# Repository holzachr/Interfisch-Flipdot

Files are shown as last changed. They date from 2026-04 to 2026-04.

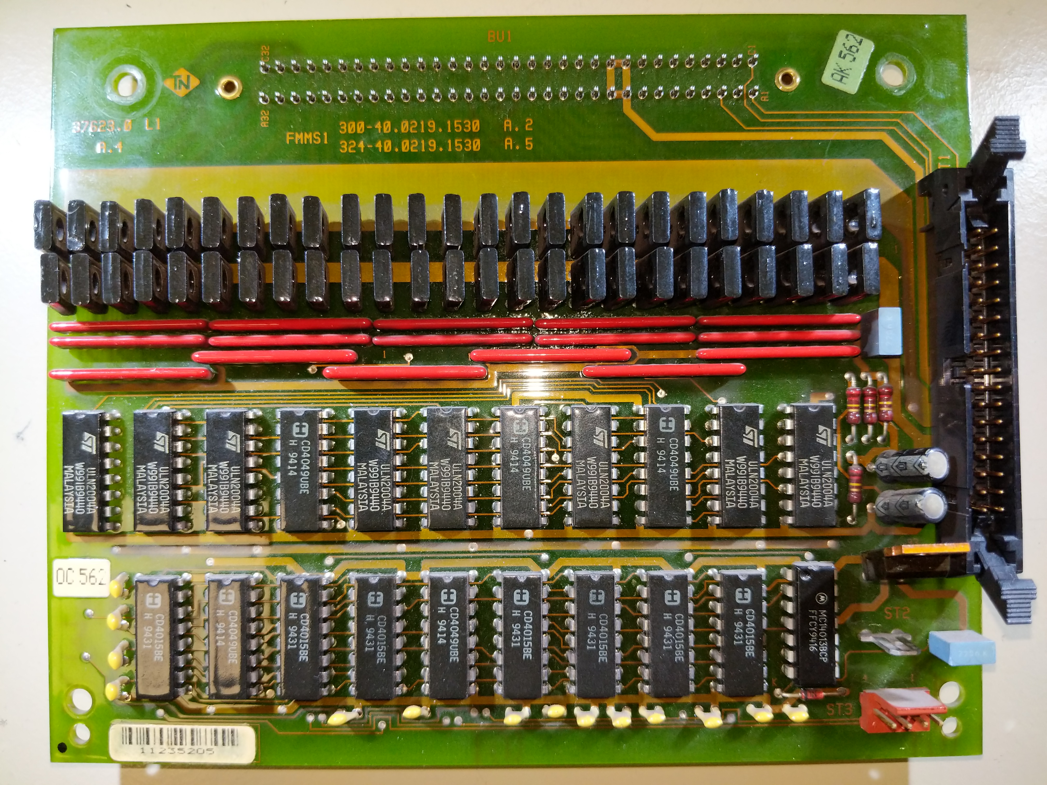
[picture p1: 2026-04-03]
reverseengeneering/annax37623_front.jpg

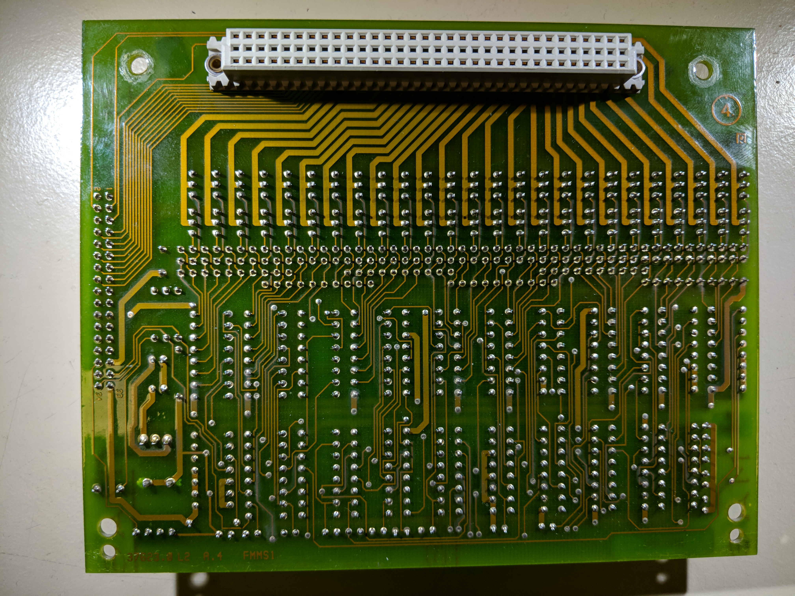
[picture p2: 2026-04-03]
reverseengeneering/annax37623_back_unlit.jpg

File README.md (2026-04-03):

This is a fork of "Interfisch"'s brilliant work for creating an ESP32 based "Annax" flipdot module controller board, software and more.

The goals of this fork are
- Re-layouting the controller board to fit the original ADtranz controller board
- Modifying the ESP32 software to support the original ADtranz flipdot module configuration (2x 25x16, 2x 20x16, 1x 25x16)
- Added another useful test pattern (checkers)
- Made flipdot timing parameters settable through MQTT, to help determine ideal settings

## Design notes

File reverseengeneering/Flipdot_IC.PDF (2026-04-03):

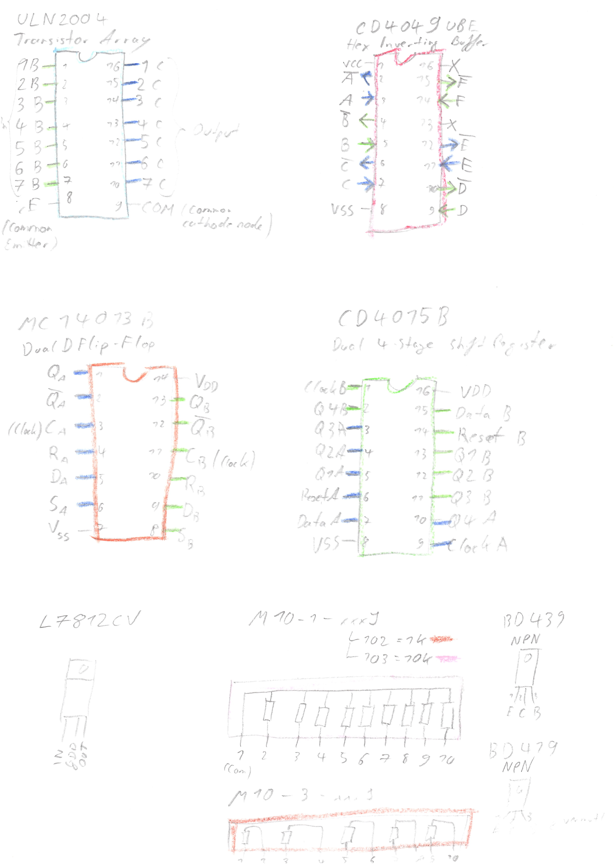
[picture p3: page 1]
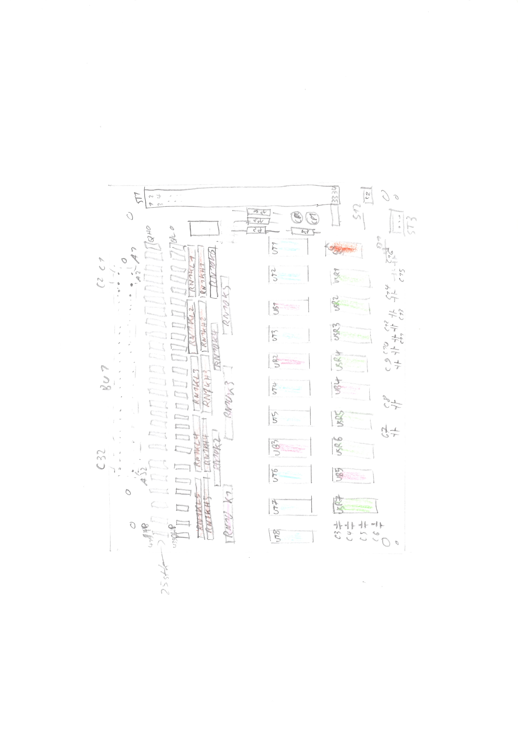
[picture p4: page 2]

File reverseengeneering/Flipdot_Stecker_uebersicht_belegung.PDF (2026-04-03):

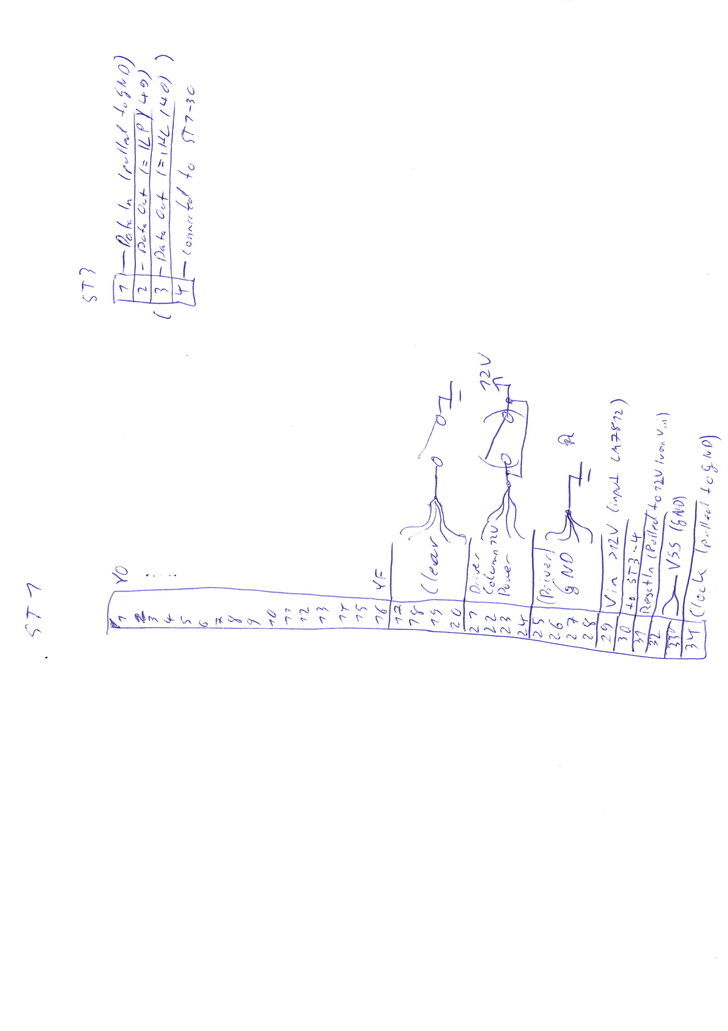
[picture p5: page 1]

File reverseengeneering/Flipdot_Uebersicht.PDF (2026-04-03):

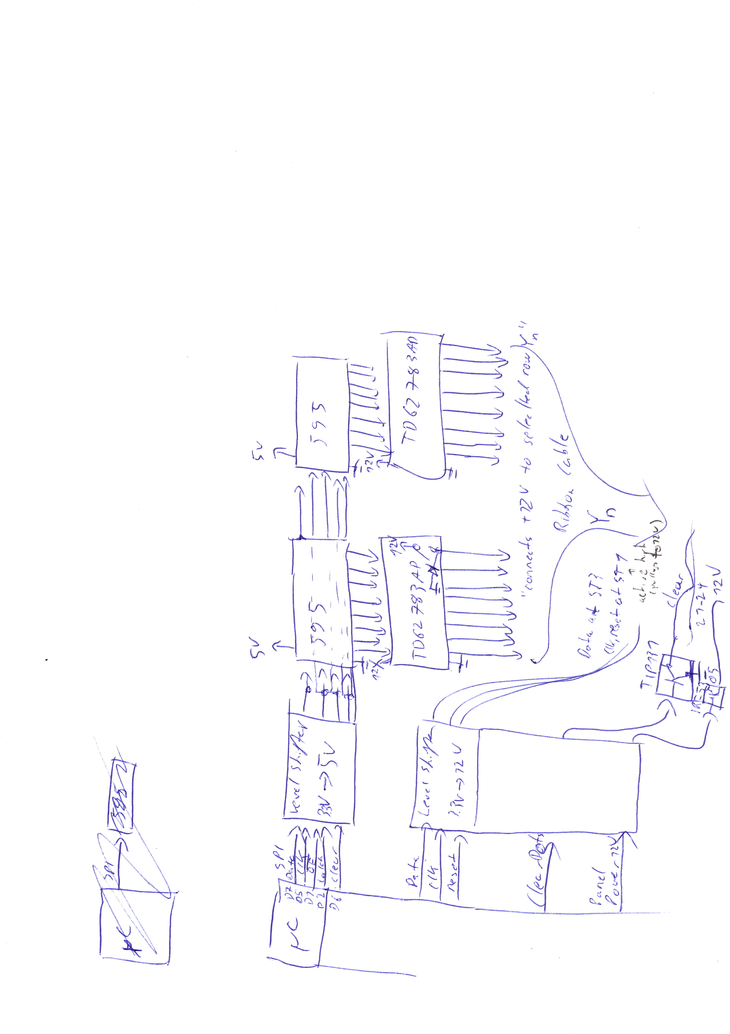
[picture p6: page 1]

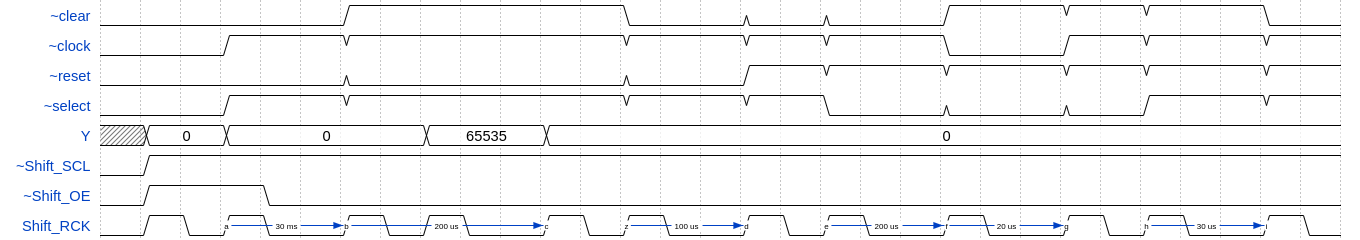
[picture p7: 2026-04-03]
reverseengeneering/control_initialize_timingdiagram_wavedrom.png

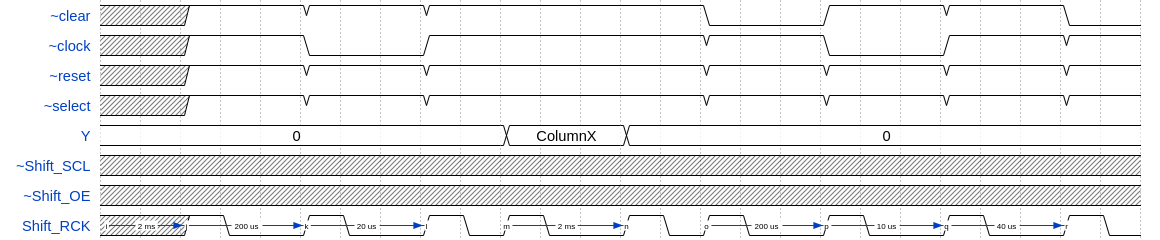
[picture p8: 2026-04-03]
reverseengeneering/control_renderColumn_timingdiagram_wavedrom.png

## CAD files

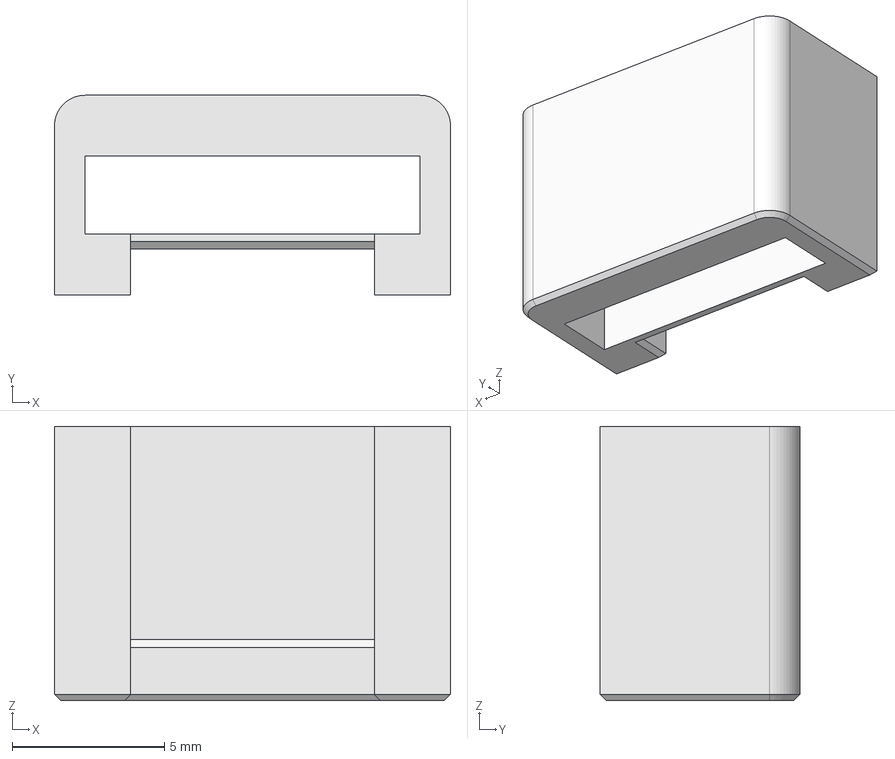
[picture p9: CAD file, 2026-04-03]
CAD/4Pin_DataConnector_Housing.FCStd
13.0 x 6.55 x 9.00 mm

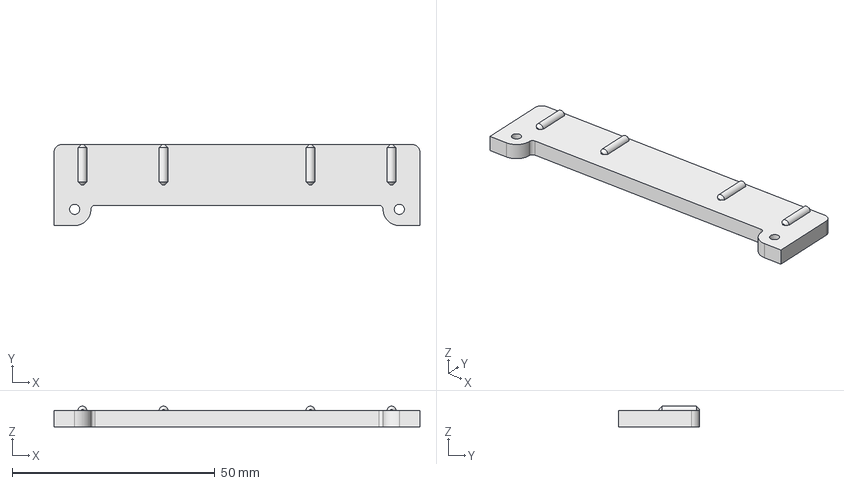
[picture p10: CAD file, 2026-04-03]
CAD/Driverboard_Case_Slotmount.step
90.2 x 20.0 x 5.10 mm

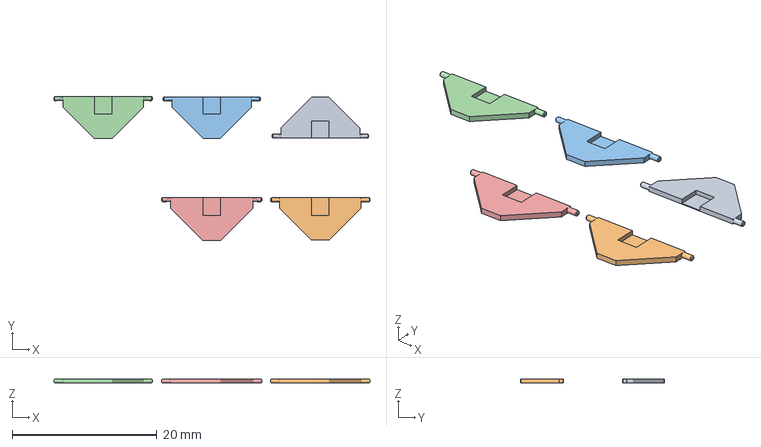
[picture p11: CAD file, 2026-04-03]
CAD/20231028_flipdot_ersatzflip_full-PartBody-95-99 %.3mf
43.6 x 19.9 x 0.594 mm
20231028_flipdot_ersatzflip_full-PartBody.stl x 5

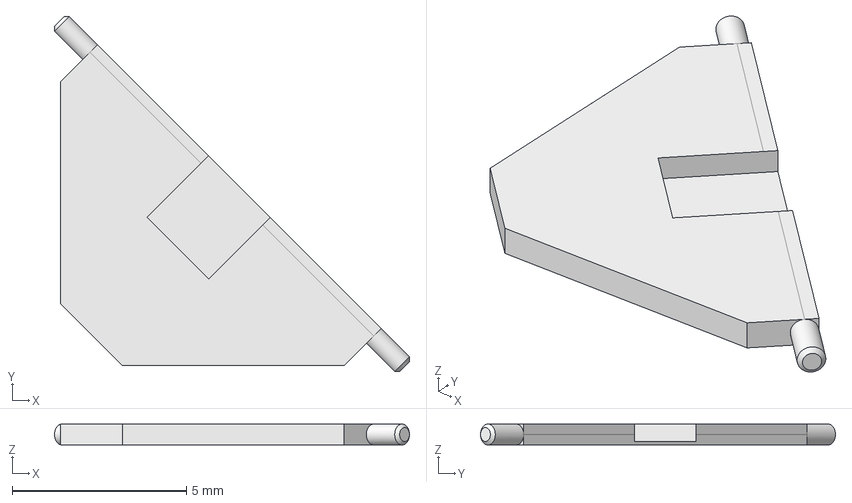
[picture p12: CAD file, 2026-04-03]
CAD/20231028_flipdot_ersatzflip_full-PartBody.step
10.2 x 10.2 x 0.6 mm

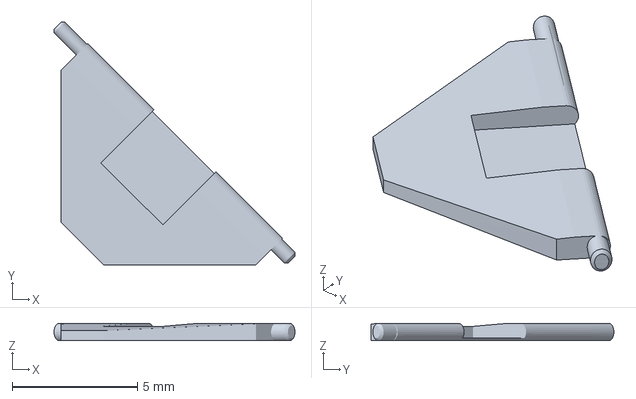
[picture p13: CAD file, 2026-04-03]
CAD/20231101_flipdot_ersatzflip_full-PartBody-100 %.3mf
9.62 x 9.69 x 0.698 mm

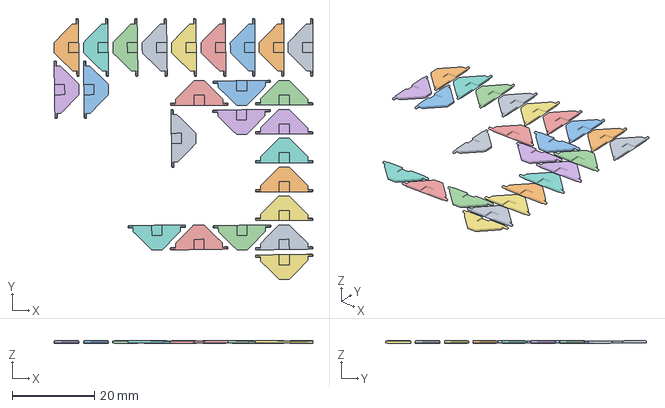
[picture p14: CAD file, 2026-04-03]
CAD/20231028_flipdot_ersatzflip_full-PartBody-100 %.3mf
62.8 x 63.2 x 0.622 mm
20231028_flipdot_ersatzflip_full-PartBody.stl x 25

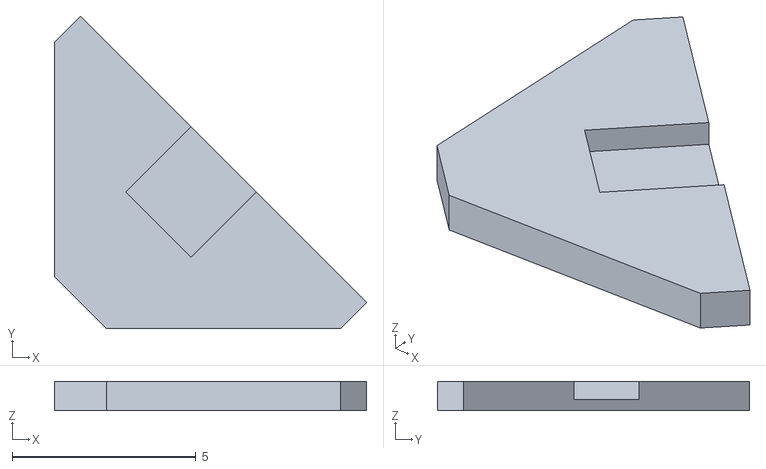
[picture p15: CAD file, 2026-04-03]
CAD/20230222_flipdot_ersatzflip-PartBody.stl
8.49 x 8.49 x 0.8

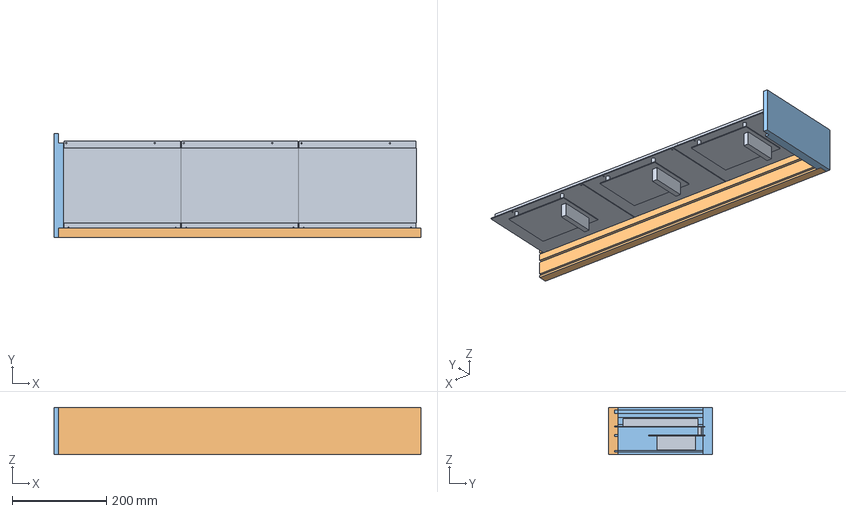
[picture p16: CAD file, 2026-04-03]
CAD/20230223_FlipdotCase.FCStd
780.0 x 220.0 x 100.0 mm
FlipdotModule
RahmenObenBody
RahmenLinksBody

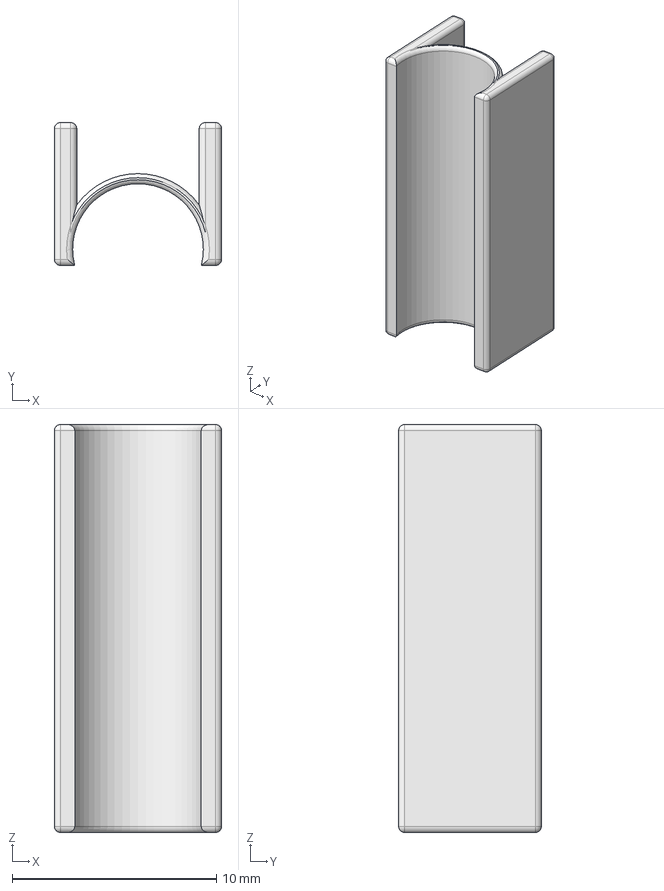
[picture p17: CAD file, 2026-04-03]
CAD/20230603_flipdot_glasclip.step
8.20 x 7.00 x 20.0 mm

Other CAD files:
CAD/4Pin_DataConnector_Housing-Part.step
CAD/20231028_flipdot_ersatzflip_full.FCStd
CAD/20231101_flipdot_ersatzflip_full-PartBody.step
CAD/20230222_flipdot_ersatzflip.FCStd
CAD/20230603_flipdot_glasclip.FCStd
CAD/20231028_flipdot_ersatzflip_full-PartBody.3mf
CAD/20231028_flipdot_ersatzflip_full-PartBody.stl
CAD/20231101_flipdot_ersatzflip_full-PartBody.stl
CAD/Driverboard_Case_Slotmount.FCStd

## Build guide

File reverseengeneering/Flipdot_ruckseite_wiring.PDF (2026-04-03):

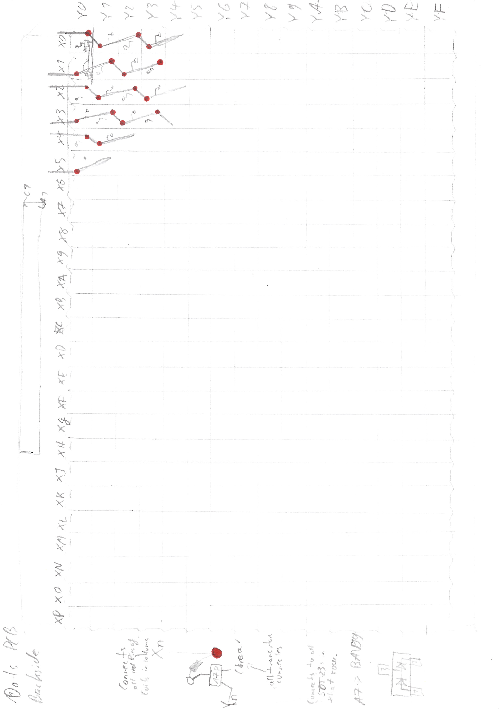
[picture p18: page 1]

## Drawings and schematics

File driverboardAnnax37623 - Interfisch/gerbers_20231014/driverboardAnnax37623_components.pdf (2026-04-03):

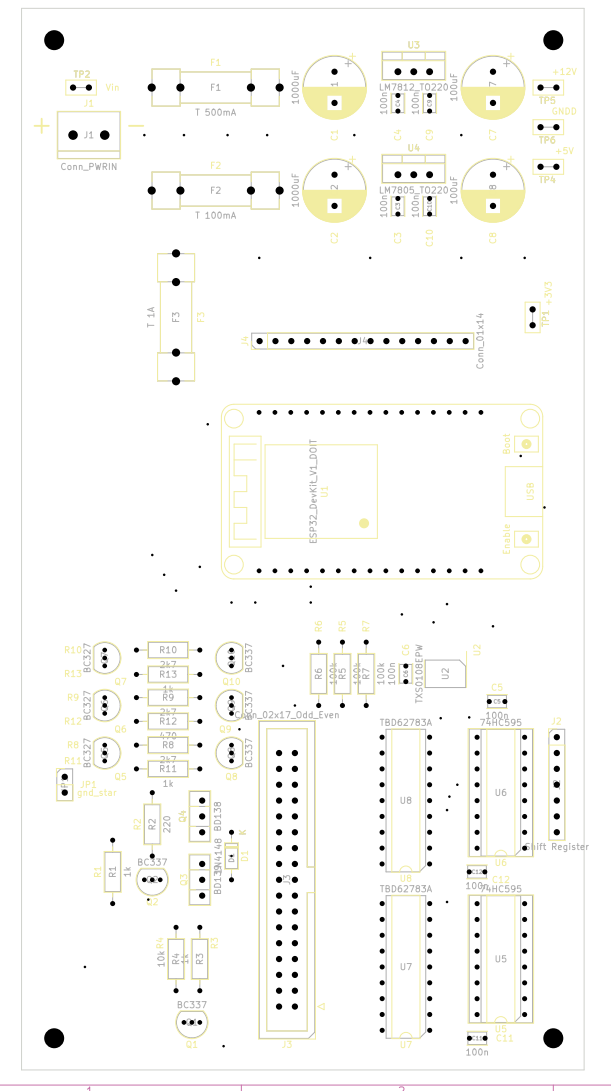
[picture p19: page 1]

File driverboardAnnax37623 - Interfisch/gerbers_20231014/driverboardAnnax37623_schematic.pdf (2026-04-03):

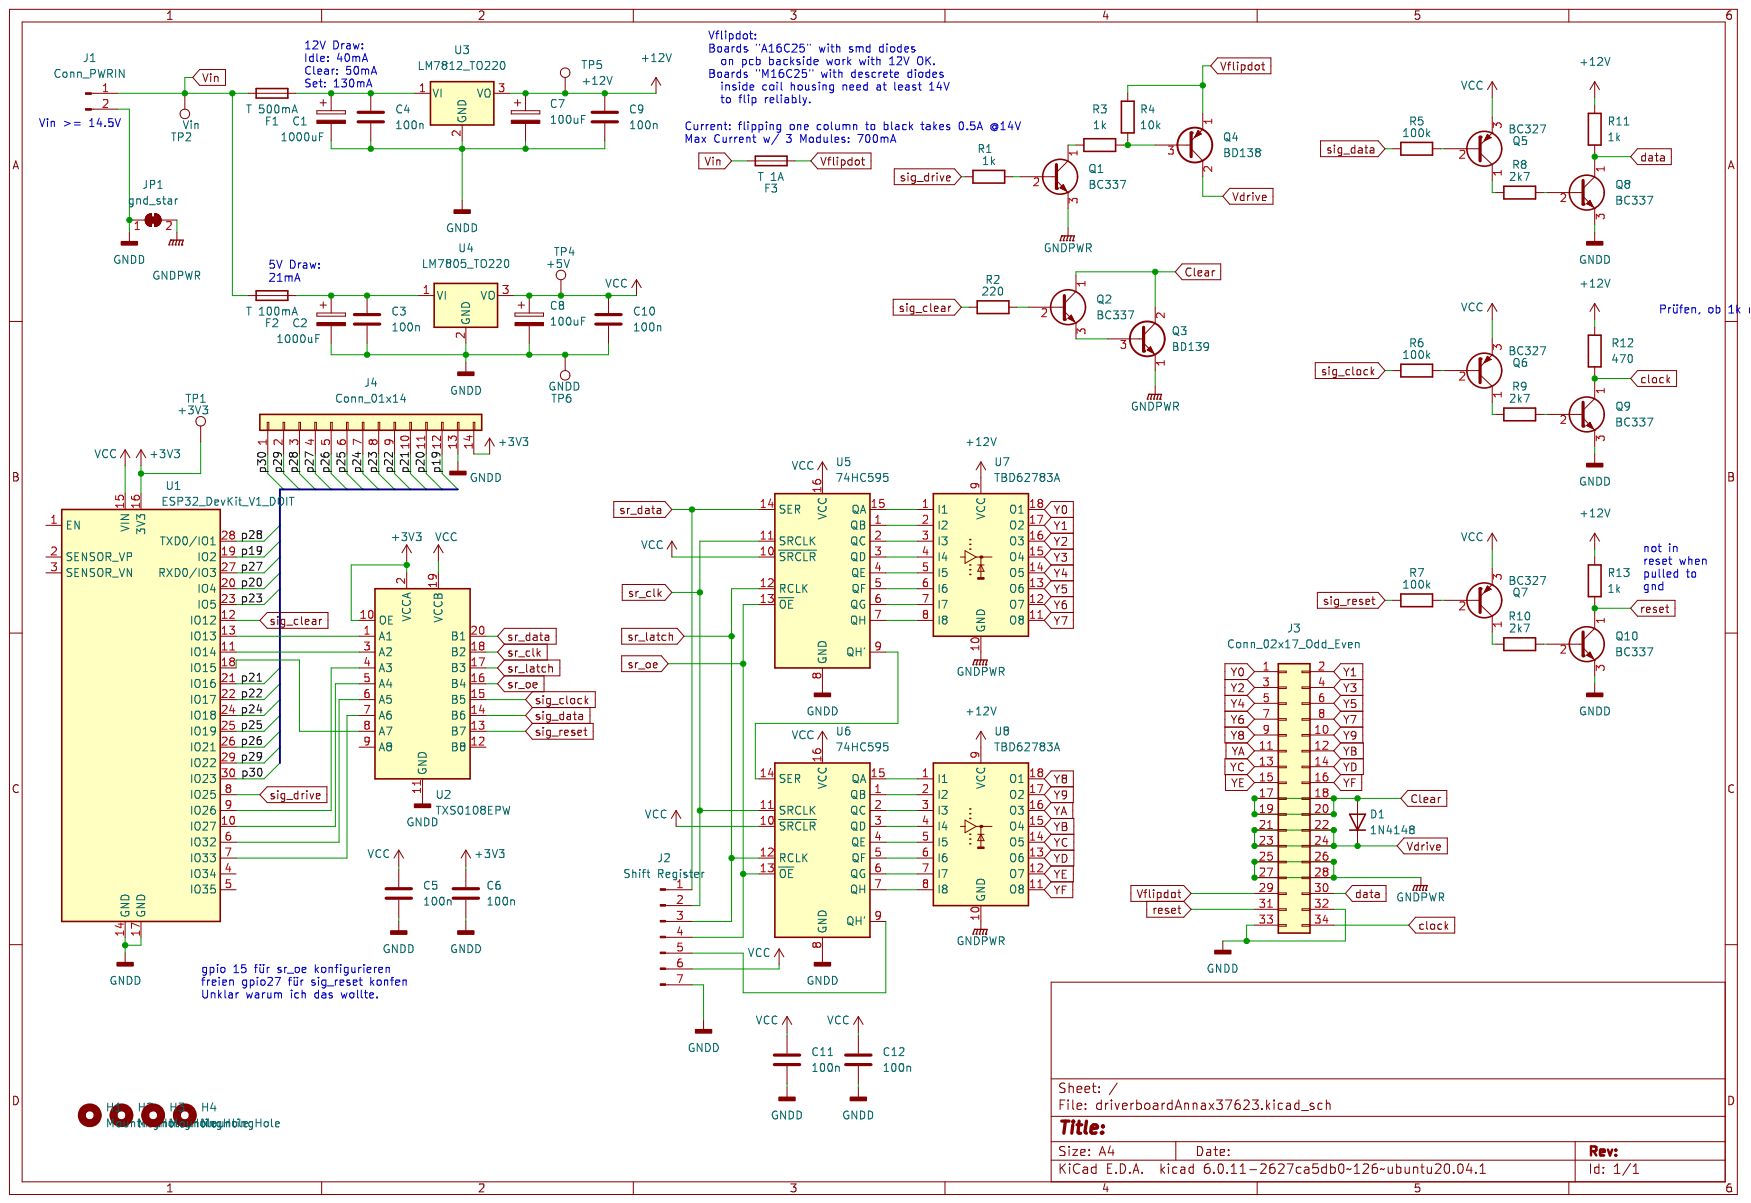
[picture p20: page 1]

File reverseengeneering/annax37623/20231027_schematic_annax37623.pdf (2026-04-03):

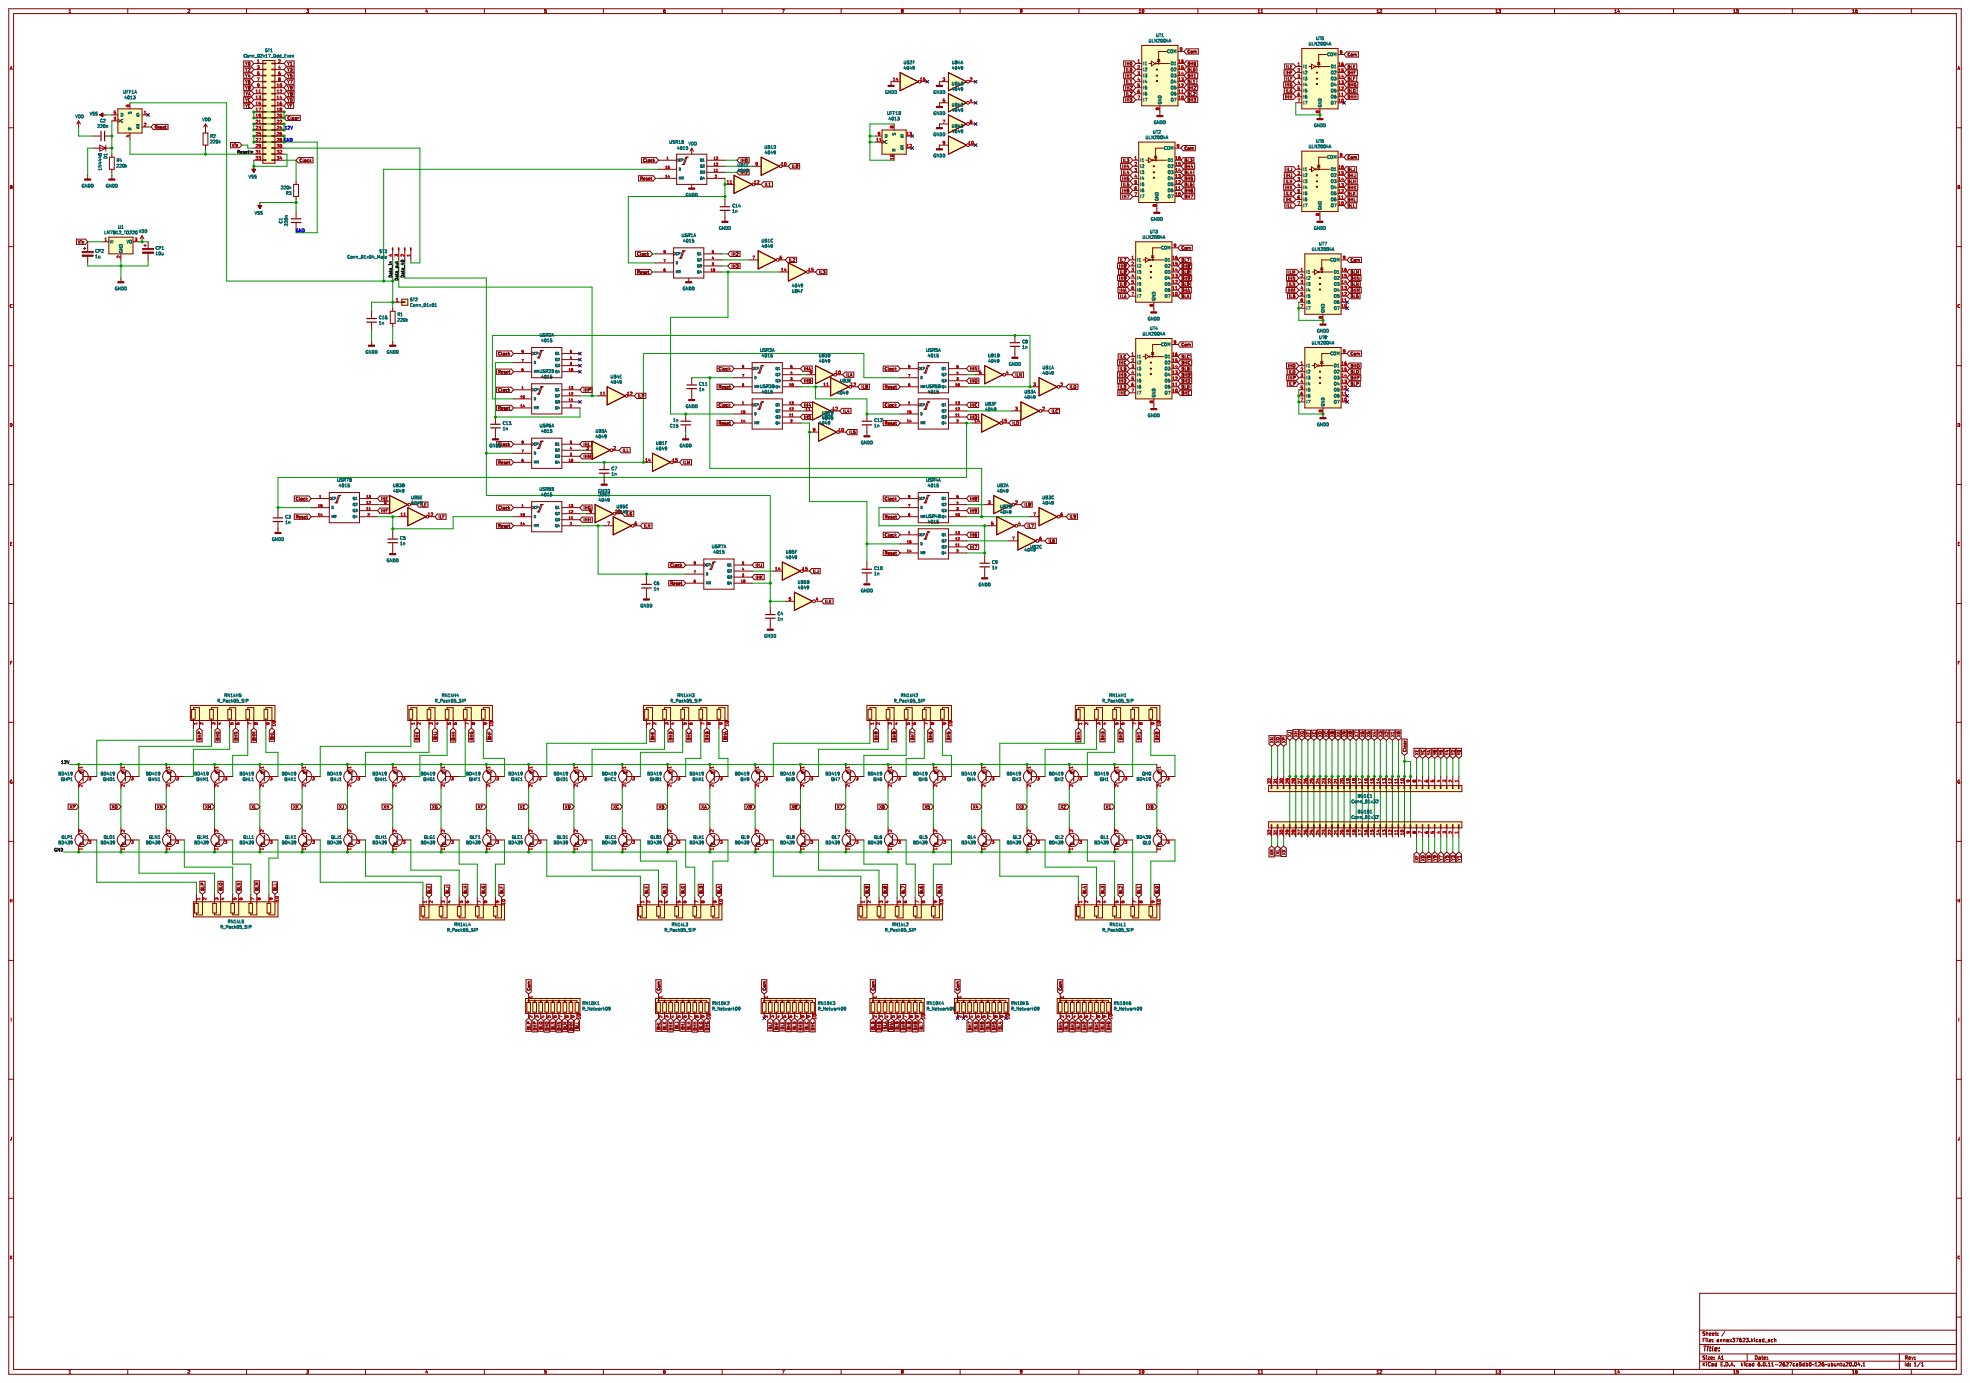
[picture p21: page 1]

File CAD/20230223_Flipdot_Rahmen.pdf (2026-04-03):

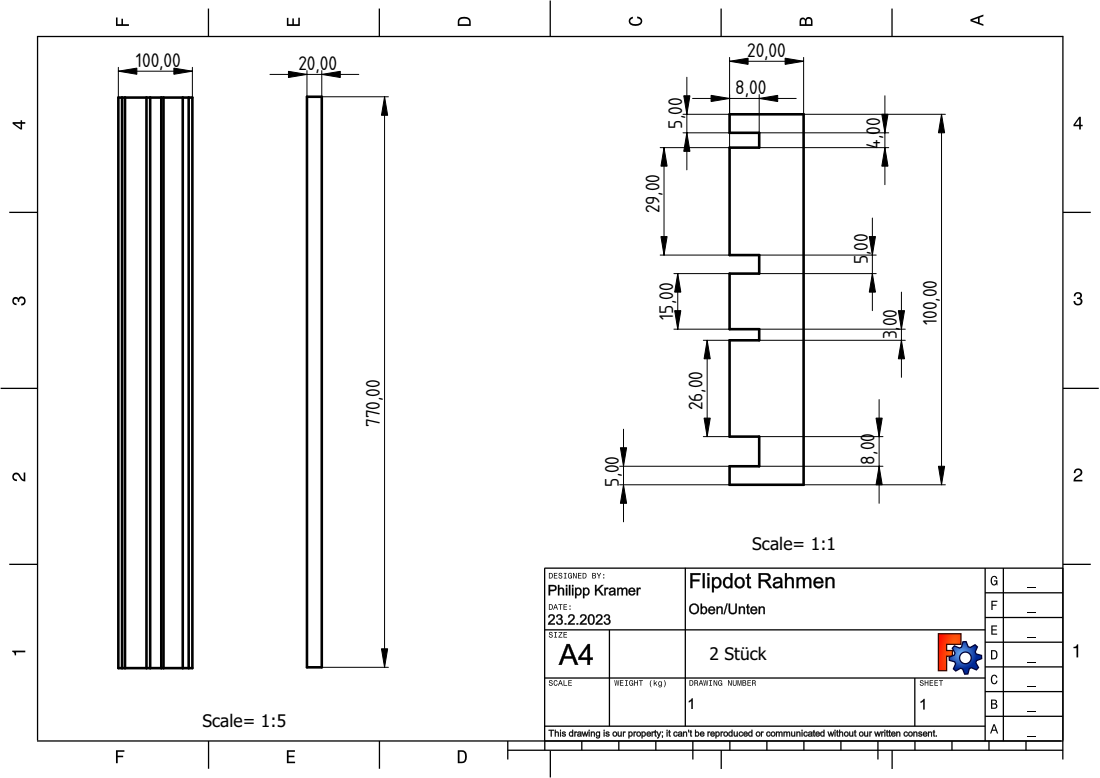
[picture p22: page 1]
ale; Stü c

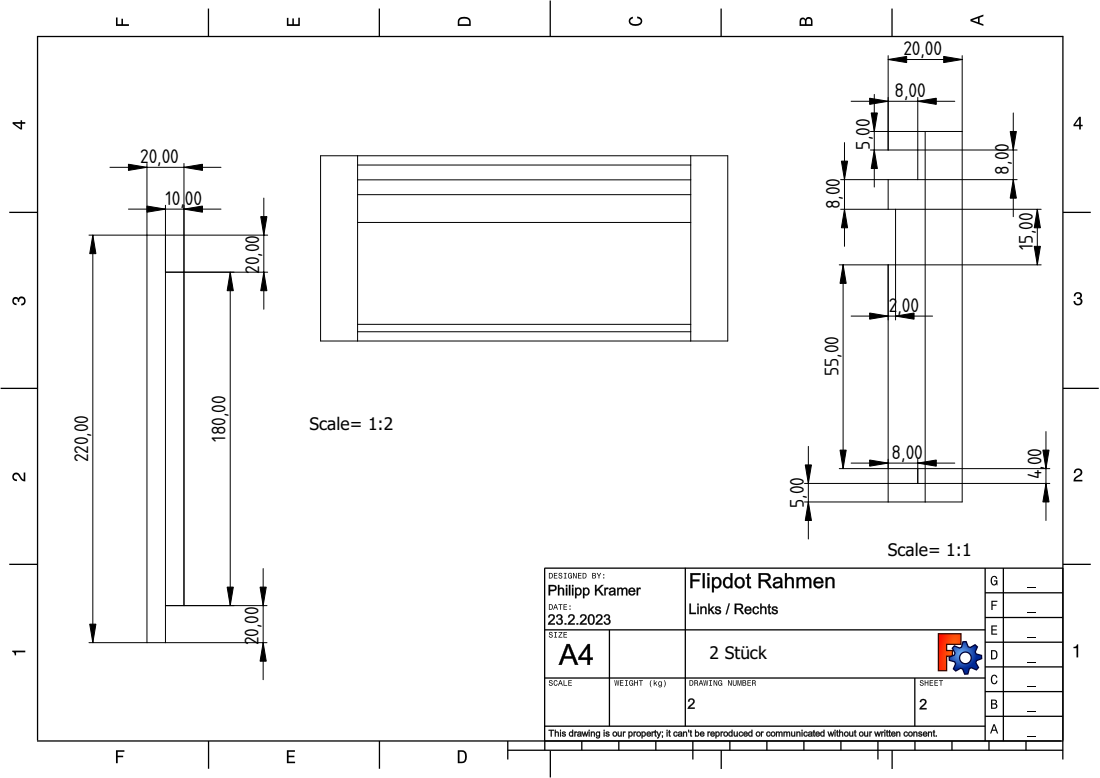
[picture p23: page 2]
ale; Stü c

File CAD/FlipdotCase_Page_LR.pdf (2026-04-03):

ale; Stü c

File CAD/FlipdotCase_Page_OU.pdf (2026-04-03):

ale; Stü c

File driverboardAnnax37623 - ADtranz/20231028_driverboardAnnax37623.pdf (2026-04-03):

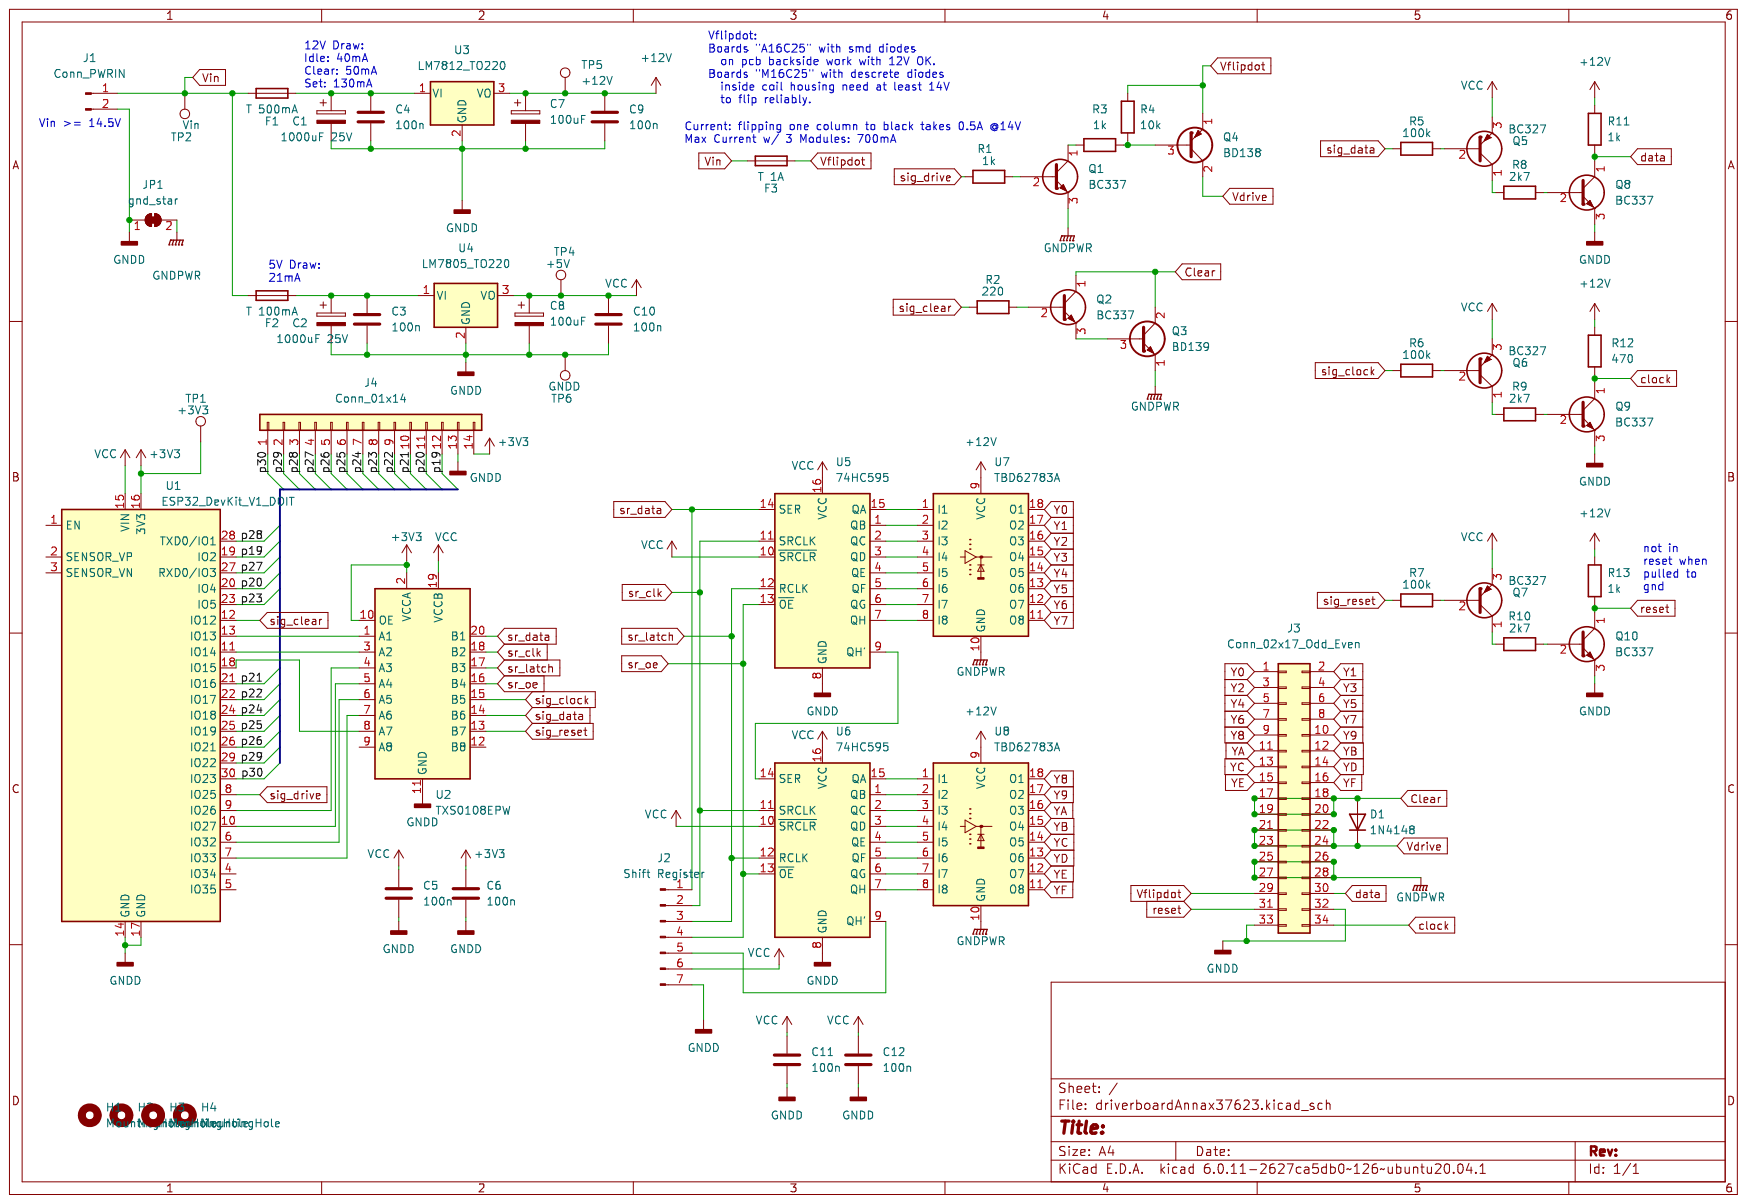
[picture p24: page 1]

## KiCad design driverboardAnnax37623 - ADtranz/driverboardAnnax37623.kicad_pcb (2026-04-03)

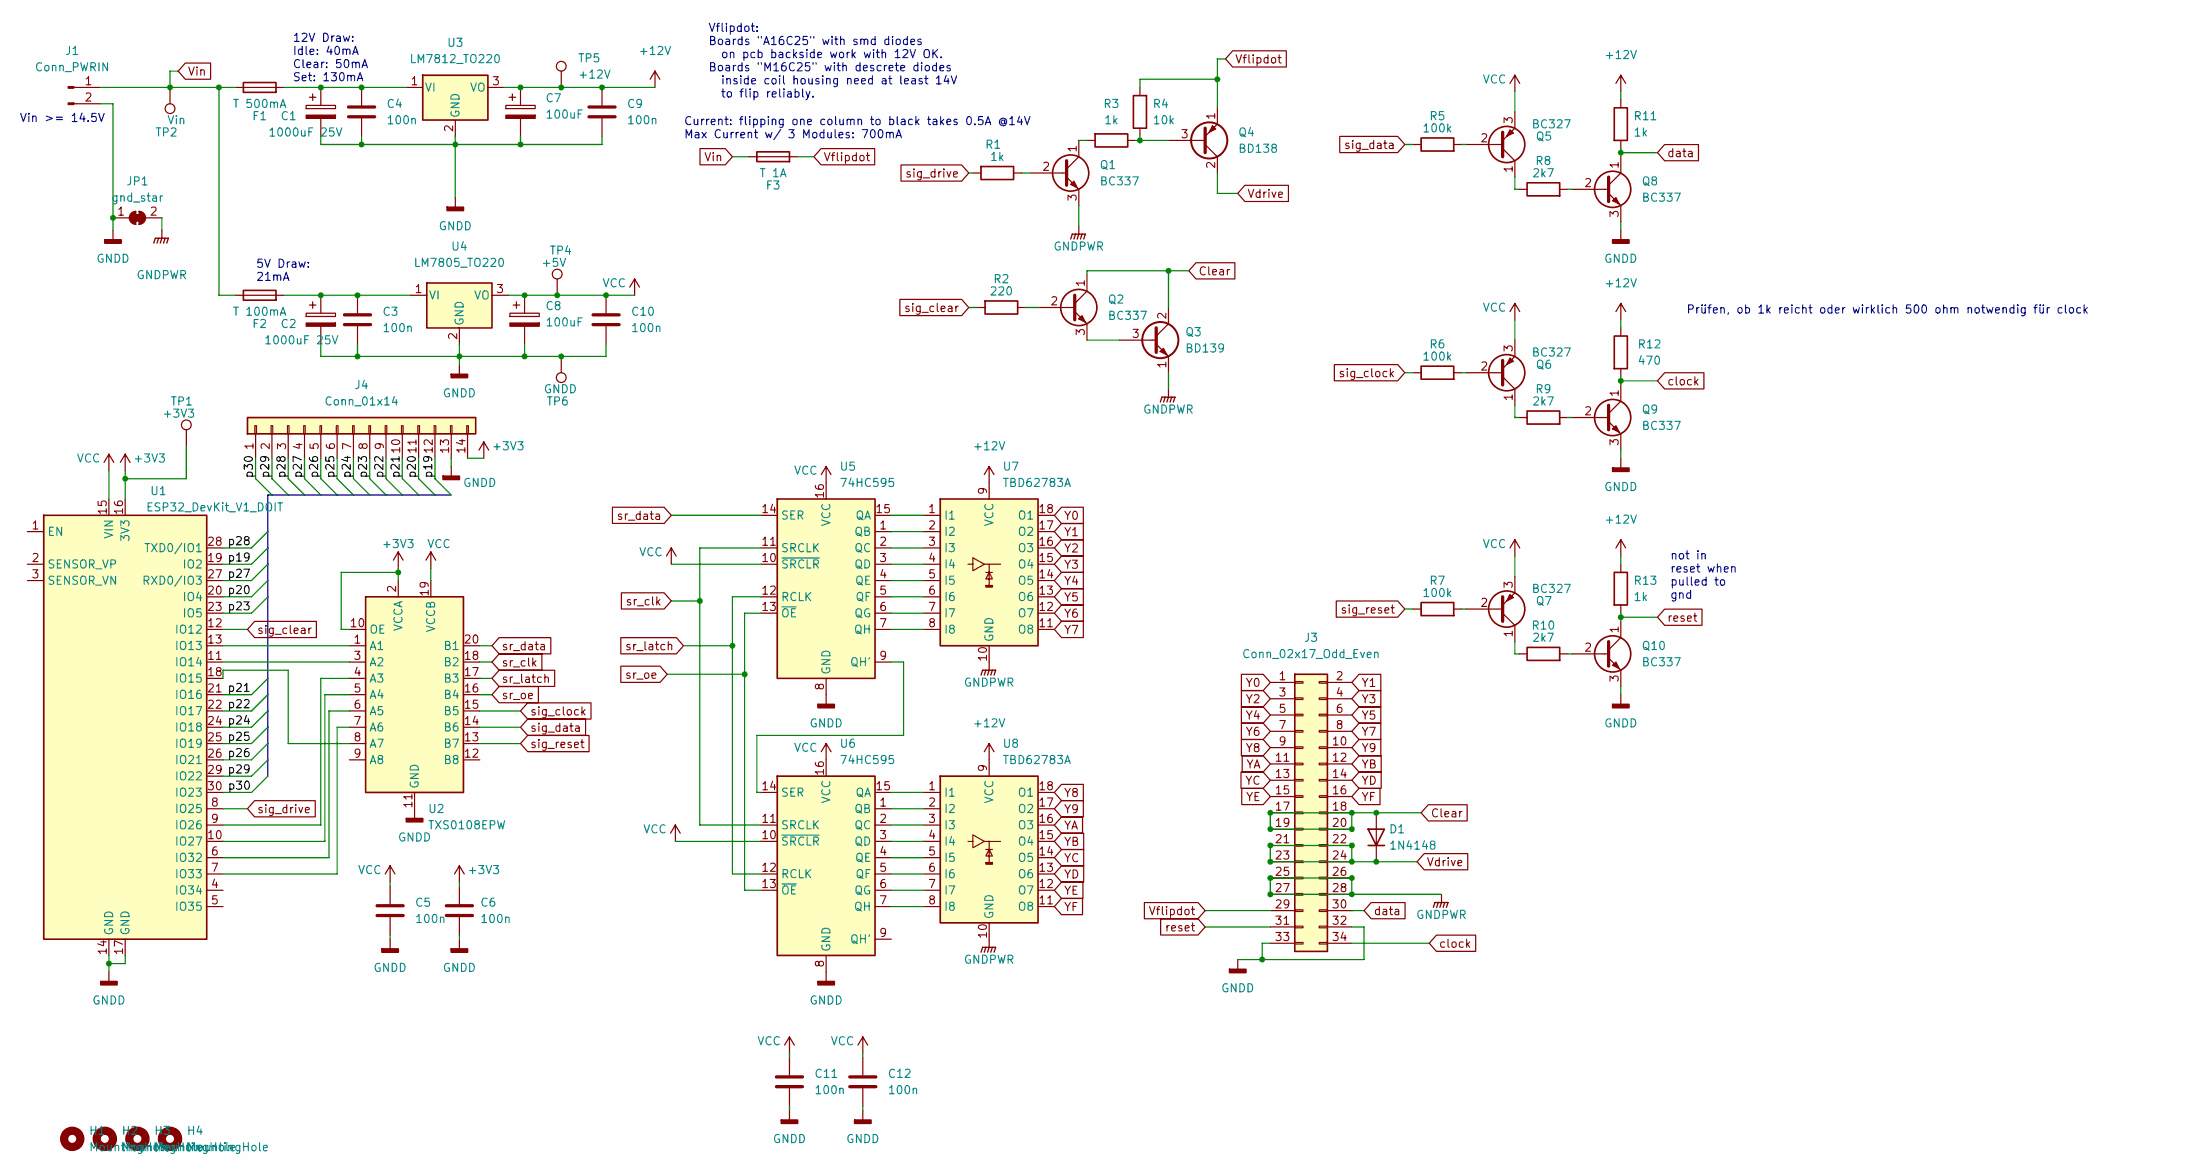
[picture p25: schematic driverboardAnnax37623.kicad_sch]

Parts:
C1, C2: 1000uF 25V; CP_Radial_D10.0mm_P5.00mm
C3, C4, C5, C6, C9, C10, C11, C12: 100n; C_Disc_D3.0mm_W2.0mm_P2.50mm
C7, C8: 100uF; CP_Radial_D10.0mm_P5.00mm
D1: 1N4148; D_DO-35_SOD27_P7.62mm_Horizontal
F1: T 500mA; Fuseholder_Clip-5x20mm_Littelfuse_100_Inline_P20.50x4.60mm_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
F2: T 100mA; Fuseholder_Clip-5x20mm_Littelfuse_100_Inline_P20.50x4.60mm_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
F3: T 1A; Fuseholder_Clip-5x20mm_Littelfuse_100_Inline_P20.50x4.60mm_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
H1, H3: MountingHole; MountingHole_4mm
H2, H4: MountingHole; MountingHole_5mm
J1: Conn_PWRIN; TerminalBlock_bornier-2_P5.08mm
J3: Conn_02x17_Odd_Even; IDC-Header_2x17_P2.54mm_Vertical
J4: Conn_01x14; PinHeader_1x14_P2.54mm_Vertical
JP1: gnd_star; PinHeader_1x02_P2.54mm_Vertical
Q1, Q2, Q8, Q9, Q10: BC337; TO-92_Inline
Q3: BD139; TO-126-3_Vertical
Q4: BD138; TO-126-3_Vertical
Q5, Q6, Q7: BC327; TO-92_Inline
R1, R3, R11, R13: 1k; R_Axial_DIN0207_L6.3mm_D2.5mm_P10.16mm_Horizontal
R2: 220; R_Axial_DIN0207_L6.3mm_D2.5mm_P10.16mm_Horizontal
R4: 10k; R_Axial_DIN0207_L6.3mm_D2.5mm_P10.16mm_Horizontal
R5, R6, R7: 100k; R_Axial_DIN0207_L6.3mm_D2.5mm_P10.16mm_Horizontal
R8, R9, R10: 2k7; R_Axial_DIN0207_L6.3mm_D2.5mm_P10.16mm_Horizontal
R12: 470; R_Axial_DIN0207_L6.3mm_D2.5mm_P10.16mm_Horizontal
TP1: +3V3; TestPoint_Bridge_Pitch2.54mm_Drill1.0mm
TP2: Vin; TestPoint_Bridge_Pitch2.54mm_Drill1.0mm
TP4: +5V; TestPoint_Bridge_Pitch2.54mm_Drill1.0mm
TP5: +12V; TestPoint_Bridge_Pitch2.54mm_Drill1.0mm
TP6: GNDD; TestPoint_Bridge_Pitch2.54mm_Drill1.0mm
U1: ESP32_DevKit_V1_DOIT; esp32_devkit_v1_doit
U2: TXS0108EPW; TSSOP-20_4.4x6.5mm_P0.65mm
U3: LM7812_TO220; TO-220-3_Vertical
U4: LM7805_TO220; TO-220-3_Vertical
U5, U6: 74HC595; DIP-16_W7.62mm_Socket_LongPads
U7, U8: TBD62783A; DIP-18_W7.62mm_LongPads

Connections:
+3V3: C6.1, J4.14, TP1.1, U1.16 (3V3), U2.2 (VCCA), U2.10 (OE)
+12V: C7.1, C9.1, R11.1, R12.1, R13.1, TP5.1, U3.3 (VO), U7.9 (VCC), U8.9 (VCC)
/p19: J4.12, U1.19 (IO2)
/p20: J4.11, U1.20 (IO4)
/p21: J4.10, U1.21 (IO16)
/p22: J4.9, U1.22 (IO17)
/p23: J4.8, U1.23 (IO5)
/p24: J4.7, U1.24 (IO18)
/p25: J4.6, U1.25 (IO19)
/p26: J4.5, U1.26 (IO21)
/p27: J4.4, U1.27 (RXD0/IO3)
/p28: J4.3, U1.28 (TXD0/IO1)
/p29: J4.2, U1.29 (IO22)
/p30: J4.1, U1.30 (IO23)
Clear: D1.2 (A), J3.17, J3.18, J3.19, J3.20, Q2.1 (C), Q3.2 (C)
GNDD: C1.2, C2.2, C3.2, C4.2, C5.2, C6.2, C7.2, C8.2, C9.2, C10.2, C11.2, C12.2, J1.2, J3.32, J3.33, J4.13, JP1.1 (A), Q8.3 (E), Q9.3 (E), Q10.3 (E), TP6.1, U1.14 (GND), U1.17 (GND), U2.11 (GND), U3.2 (GND), U4.2 (GND), U5.8 (GND), U6.8 (GND)
GNDPWR: J3.25, J3.26, J3.27, J3.28, JP1.2 (B), Q1.3 (E), Q3.1 (E), U7.10 (GND), U8.10 (GND)
unnamed: Q1.2 (B), R1.1
unnamed: Q1.1 (C), R3.2
unnamed: Q2.2 (B), R2.1
unnamed: Q2.3 (E), Q3.3 (B)
unnamed: Q4.3 (B), R3.1, R4.1
unnamed: Q5.2 (B), R5.2
unnamed: Q5.1 (C), R8.1
unnamed: Q6.2 (B), R6.2
unnamed: Q6.1 (C), R9.1
unnamed: Q7.2 (B), R7.2
unnamed: Q7.1 (C), R10.1
unnamed: Q8.2 (B), R8.2
unnamed: Q9.2 (B), R9.2
unnamed: Q10.2 (B), R10.2
unnamed: U1.13 (IO13), U2.1 (A1)
unnamed: U1.11 (IO14), U2.3 (A2)
unnamed: U1.18 (IO15), U2.8 (A7)
unnamed: U1.9 (IO26), U2.4 (A3)
unnamed: U1.10 (IO27), U2.5 (A4)
unnamed: U1.6 (IO32), U2.6 (A5)
unnamed: U1.7 (IO33), U2.7 (A6)
unnamed: C1.1, C4.1, F1.2, U3.1 (VI)
unnamed: C2.1, C3.1, F2.2, U4.1 (VI)
unnamed: U5.15 (QA), U7.1 (I1)
unnamed: U5.1 (QB), U7.2 (I2)
unnamed: U5.2 (QC), U7.3 (I3)
unnamed: U5.3 (QD), U7.4 (I4)
unnamed: U5.4 (QE), U7.5 (I5)
unnamed: U5.5 (QF), U7.6 (I6)
unnamed: U5.6 (QG), U7.7 (I7)
unnamed: U5.9 (QH'), U6.14 (SER)
unnamed: U5.7 (QH), U7.8 (I8)
unnamed: U6.15 (QA), U8.1 (I1)
unnamed: U6.1 (QB), U8.2 (I2)
unnamed: U6.2 (QC), U8.3 (I3)
unnamed: U6.3 (QD), U8.4 (I4)
unnamed: U6.4 (QE), U8.5 (I5)
unnamed: U6.5 (QF), U8.6 (I6)
unnamed: U6.6 (QG), U8.7 (I7)
unnamed: U6.7 (QH), U8.8 (I8)
VCC: C5.1, C8.1, C10.1, C11.1, C12.1, Q5.3 (E), Q6.3 (E), Q7.3 (E), TP4.1, U1.15 (VIN), U2.19 (VCCB), U4.3 (VO), U5.10 (~SRCLR), U5.16 (VCC), U6.10 (~SRCLR), U6.16 (VCC)
Vdrive: D1.1 (K), J3.21, J3.22, J3.23, J3.24, Q4.2 (C)
Vflipdot: F3.2, J3.29, Q4.1 (E), R4.2
Vin: F1.1, F2.1, F3.1, J1.1, TP2.1
Y0: J3.1, U7.18 (O1)
Y1: J3.2, U7.17 (O2)
Y2: J3.3, U7.16 (O3)
Y3: J3.4, U7.15 (O4)
Y4: J3.5, U7.14 (O5)
Y5: J3.6, U7.13 (O6)
Y6: J3.7, U7.12 (O7)
Y7: J3.8, U7.11 (O8)
Y8: J3.9, U8.18 (O1)
Y9: J3.10, U8.17 (O2)
YA: J3.11, U8.16 (O3)
YB: J3.12, U8.15 (O4)
YC: J3.13, U8.14 (O5)
YD: J3.14, U8.13 (O6)
YE: J3.15, U8.12 (O7)
YF: J3.16, U8.11 (O8)
clock: J3.34, Q9.1 (C), R12.2
data: J3.30, Q8.1 (C), R11.2
reset: J3.31, Q10.1 (C), R13.2
sig_clear: R2.2, U1.12 (IO12)
sig_clock: R6.1, U2.15 (B5)
sig_data: R5.1, U2.14 (B6)
sig_drive: R1.2, U1.8 (IO25)
sig_reset: R7.1, U2.13 (B7)
sr_clk: U2.18 (B2), U5.11 (SRCLK), U6.11 (SRCLK)
sr_data: U2.20 (B1), U5.14 (SER)
sr_latch: U2.17 (B3), U5.12 (RCLK), U6.12 (RCLK)
sr_oe: U2.16 (B4), U5.13 (~OE), U6.13 (~OE)

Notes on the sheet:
Vin >= 14.5V
5V Draw: 21mA
not in reset when pulled to gnd
Current: flipping one column to black takes 0.5A @14V Max Current w/ 3 Modules: 700mA
Prüfen, ob 1k reicht oder wirklich 500 ohm notwendig für clock
Vflipdot: Boards "A16C25" with smd diodes on pcb backside work with 12V OK. Boards "M16C25" with descrete diodes inside coil housing need at least 14V to flip reliably.
12V Draw: Idle: 40mA Clear: 50mA Set: 130mA

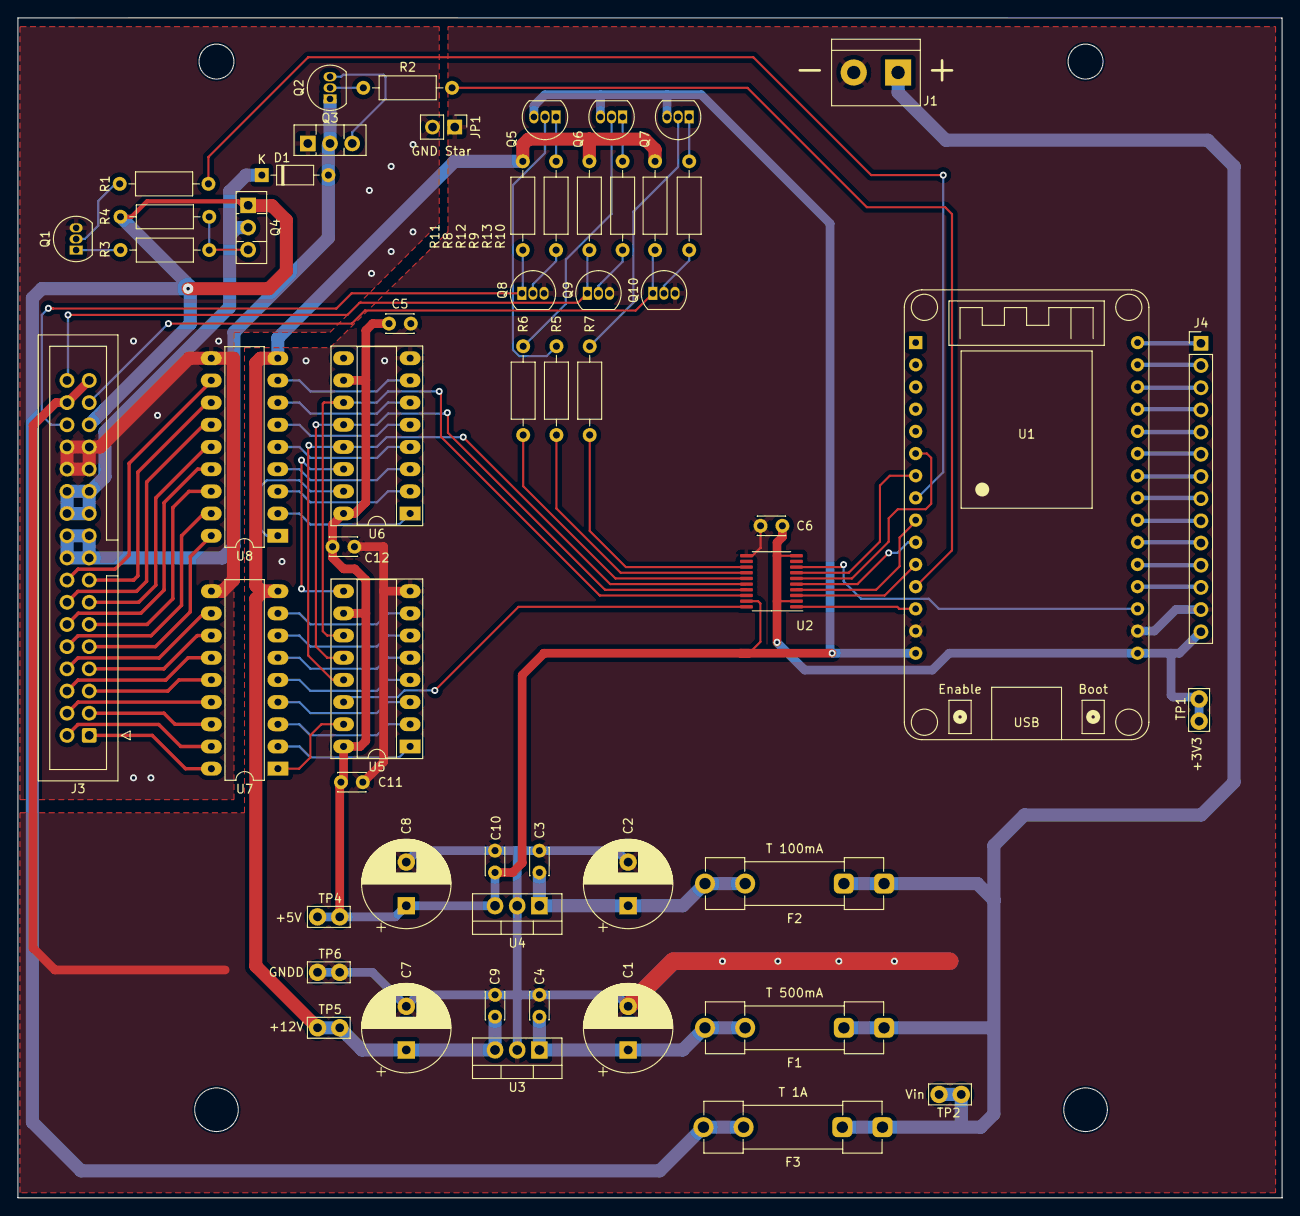
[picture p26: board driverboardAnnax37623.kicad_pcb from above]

Board: 2 copper layers, 144.7 x 135.1 mm, 60 parts (0 on the bottom side), 89 nets.

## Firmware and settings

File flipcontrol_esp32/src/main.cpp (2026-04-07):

#include <Arduino.h>
#include <Homie.h>

HomieNode displayNode("display", "Display", "display");
HomieNode settingsNode("settings", "Settings", "settings");
HomieNode resultNode("result", "Result", "result");

#include "flipdot.h"
#include "image.h"


Image flip;

unsigned long loopmillis=0;
unsigned long last_update=0;

bool clearFirst=true;
bool optimizeClear=false;
bool optimizeSet=true;
bool firstDraw = true;

uint8_t stringToBool(String s);

bool presetHandler(const HomieRange& range, const String& value);
bool orderHandler(const HomieRange& range, const String& value);
bool dataHandler(const HomieRange& range, const String& value);
bool controlHandler(const HomieRange& range, const String& value);
bool textHandler(const HomieRange& range, const String& value) ;
bool textLargeHandler(const HomieRange& range, const String& value) ;

bool clearFirstHandler(const HomieRange& range, const String& value);
bool optimizeClearHandler(const HomieRange& range, const String& value);
bool optimizeSetHandler(const HomieRange& range, const String& value);
bool driveDotSetDelayUsHandler(const HomieRange& range, const String& value);
bool driveDotClearDelayUsHandler(const HomieRange& range, const String& value);
bool shiftDelayUsHandler(const HomieRange& range, const String& value);
bool shiftLatchTimeUsHandler(const HomieRange& range, const String& value);

String error; //used to buffer error messages to be send via mqtt

void setup() {
    flip.init();
    flip.setDisplayMirror(false, false); //true,true=mirror both axis (rotate 180deg)

    Serial.begin(115200);

    // Setup Homie
    Homie_setFirmware("flipdot", "0.1.2");
    displayNode.advertise("preset").settable(presetHandler);
    displayNode.advertise("data").settable(dataHandler);
    displayNode.advertise("order").settable(orderHandler);
    displayNode.advertise("control").settable(controlHandler);
    displayNode.advertise("text").settable(textHandler);
    displayNode.advertise("textlarge").settable(textLargeHandler);
    settingsNode.advertise("clearfirst").settable(clearFirstHandler);
    settingsNode.advertise("optimizeclear").settable(optimizeClearHandler);
    settingsNode.advertise("optimizeset").settable(optimizeSetHandler);
    settingsNode.advertise("driveDotSetDelayUs").settable(driveDotSetDelayUsHandler);
    settingsNode.advertise("driveDotClearDelayUs").settable(driveDotClearDelayUsHandler);
    settingsNode.advertise("shiftDelayUs").settable(shiftDelayUsHandler);
    settingsNode.advertise("shiftLatchTimeUs").settable(shiftLatchTimeUsHandler);
   
    Homie.setup();

    error="";
}


void loop() {
    Homie.loop();
    loopmillis = millis();
    
    static unsigned long last_change=0;

    UpdateReturn result;
    if (firstDraw)
    {
        // Uncertain state after power-up, clear everything
        UpdateReturn result = flip.updateByColumn(true, false, false); //0=not finished, 1=finished        
    }
    else
    {
        // Certain state after first draw, use optimizeClear / optimizeSet
        UpdateReturn result = flip.updateByColumn(clearFirst, optimizeClear, optimizeSet); //0=not finished, 1=finished
    }    

    static UpdateReturn last_result = finished;
    if (last_result == nochange && result != last_result) { //was finished but has just started updating again
        last_change = loopmillis; //display started changing dots. set starting time.
    }
    last_result = result;
    if (result == finished) //just finished
    {
        firstDraw = false;
        unsigned long duration=millis()-last_change;
        Serial.print("Last Change took "); Serial.print(duration); Serial.println(" ms");
        Serial.print("Update max took "); Serial.print(flip.updateDuration); Serial.println(" ms");
        resultNode.setProperty("duration").send((String)duration);
        resultNode.setProperty("updateduration").send((String)flip.updateDuration);
        flip.updateDuration=0; //reset
    }

    if (error.length()>0) { //is there an error to send?
        resultNode.setProperty("error").send(error);
        error=""; //clear
    }    
}


bool orderHandler(const HomieRange& range, const String& value) 
{
    Serial.print("Order payload="); Serial.println(value);

    if (value=="ascending") 
        flip.resetOrder(true);
    else if (value=="descending") 
        flip.resetOrder(false);
    else if (value=="shuffle")
        flip.shuffleOrder(8);
    else if (value=="random")
        flip.shuffleOrder(flip.getW());
    else
        return false;

    displayNode.setProperty("order").send(value);
    return true;    
}

bool presetHandler(const HomieRange& range, const String& value) 
{
    Serial.print("Preset payload="); Serial.println(value);

    if (value == "white"){
        flip.setBuffer_solid(1);
        Homie.getLogger() << "Preset is White" << endl;
    }else if(value == "black"){
        flip.setBuffer_solid(0);
        Homie.getLogger() << "Preset is Black" << endl;
    }else if(value == "stripes"){
        flip.setBuffer_Preset_Stripes();
        Homie.getLogger() << "Preset is stripes" << endl;
    }else if(value == "checkers"){
        flip.setBuffer_Preset_Checkers();
        Homie.getLogger() << "Preset is checkers" << endl;
    }else if(value == "checkers-inverse"){
        flip.setBuffer_Preset_CheckersInverse();
        Homie.getLogger() << "Preset is checkers-inverse" << endl;
    }else if(value == "random"){
        flip.setBuffer_random(50);
    }else if(value == "uptime") {
        flip.setBuffer_solid(0);
        flip.addBuffer_text((String)(millis()/1000),0,0);
    }else{
        error="preset \""+value+"\" not found";
        return false;
    }

    displayNode.setProperty("preset").send(value);

    return true;
}

bool dataHandler(const HomieRange& range, const String& value) 
{
    Serial.print("Data Received: "); Serial.println(value);
    Serial.print("Length: "); Serial.println(value.length());
    /*payload can be either be Binary/String:
     "10101101011010.." 
     "1  111 11 11 1 1..."
     "a_aa_aa_aa_aa__a_a_a.."

     Or Int (unsigned 16 bit. comma separated for each column)
     "837491,12347,592,920,114,0,12,45125,..."
    */
    if (value.length() == flip.getW() * flip.getH()) { //if characters matches pixels then its likely binary
        Serial.println("Using byString");
        flip.setBuffer_byString(value,error);
    }else{
        Serial.println("Using byInt");
        flip.setBuffer_byInt(value,error);
    }    
    
    return true;   
}

bool clearFirstHandler(const HomieRange& range, const String& value) 
{
    Serial.print("clearFirstHandler payload="); Serial.println(value);

    uint8_t res=stringToBool(value);
    if (res==0)
        clearFirst=false;
    else if(res==1)
        clearFirst=true;
    else
    {
        error="no valid input";
        return false;
    }

    settingsNode.setProperty("clearfirst").send((String)res);

    return true;
}

bool optimizeClearHandler(const HomieRange& range, const String& value) {
    Serial.print("OptimizeClearHandler payload="); Serial.println(value);
    uint8_t res=stringToBool(value);
    if (res==0){
        optimizeClear=false;
    }else if(res==1){
        optimizeClear=true;
    }else{
        error="no valid input";
        return false;
    }
    settingsNode.setProperty("optimizeclear").send((String)res);
    return true;
}

bool optimizeSetHandler(const HomieRange& range, const String& value) {
    Serial.print("OptimizeSetHandler payload="); Serial.println(value);
    uint8_t res=stringToBool(value);
    if (res==0){
        optimizeSet=false;
    }else if(res==1){
        optimizeSet=true;
    }else{
        error="no valid input";
        return false;
    }
    settingsNode.setProperty("optimizeset").send((String)res);
    return true;
}

bool driveDotSetDelayUsHandler(const HomieRange& range, const String& value) {
    Serial.print("driveDotSetDelayUsHandler payload="); Serial.println(value);
    uint16_t res = value.toInt();
    flip.flipdot.setDriveDotSetDelayUs(res);
    settingsNode.setProperty("driveDotSetDelayUs").send((String)res);
    return true;
}

bool driveDotClearDelayUsHandler(const HomieRange& range, const String& value) {
    Serial.print("driveDotClearDelayUsHandler payload="); Serial.println(value);
    uint16_t res = value.toInt();
    flip.flipdot.setDriveDotClearDelayUs(res);
    settingsNode.setProperty("driveDotClearDelayUs").send((String)res);
    return true;
}

bool shiftDelayUsHandler(const HomieRange& range, const String& value) {
    Serial.print("driveDotClearDelayUsHandler payload="); Serial.println(value);
    uint16_t res = value.toInt();
    flip.flipdot.setShiftDelayUs(res);
    settingsNode.setProperty("shiftDelayUs").send((String)res);
    return true;
}

bool shiftLatchTimeUsHandler(const HomieRange& range, const String& value) {
    Serial.print("shiftDelayUs payload="); Serial.println(value);
    uint16_t res = value.toInt();
    flip.flipdot.setShiftLatchTimeUs(res);
    settingsNode.setProperty("shiftLatchTimeUs").send((String)res);
    return true;
}


uint8_t stringToBool(String s) {
    String param=s;
    param.toLowerCase();
    if (param == "true" ||  param == "1" || param == "on" || param == "yes" || param == "y"){
        return 1;
    }else if(param == "false" || param == "0" || param == "off" || param== "no" || param == "n"){
        return 0;
    }else{
        return 2;
    }
}
 



bool controlHandler(const HomieRange& range, const String& value) {
    Serial.print("Control payload="); Serial.println(value);
    if (value == "redraw"){
        flip.redraw();
    }else if(value == "black"){
        flip.setBuffer_solid(0);
        flip.redraw();
    }else{
        error="preset \""+value+"\" not found";
        return false;
    }

  displayNode.setProperty("control").send(value);

  return true;
}

bool textHandler(const HomieRange& range, const String& value) 
{
    Serial.print("Text payload="); Serial.println(value);

    String row1;
    String row2;

    uint8_t linebreakindex = value.indexOf("\n"); //search for "\n" in string. 255 if not found
    Serial.print("Linebreakindex="); Serial.println(linebreakindex);
    if (linebreakindex!=255)  //found linebreak
    {
        row1=value.substring(0,linebreakindex);
        row2=value.substring(linebreakindex+1);
    }
    else
    {
        row1=value.substring(0, flip.getW()/6);
        row2=value.substring(flip.getW()/6);
        row2.trim(); //remove leading and trailing whitespaces
        String overflow = row2.substring(flip.getW()/6); //save text that did not fit
        row2 = row2.substring(0, flip.getW()/6);

        if (overflow.length() > 0) 
        {
            error="Text overflow:"+overflow;
            Serial.println("Text overflow");
        }
    }

    Serial.print("Row1="); Serial.println(row1);
    Serial.print("Row2="); Serial.println(row2);
    
    flip.setBuffer_solid(0); //clear

    if (row2.length() <= 0)
    {
        Serial.println("Only one row");
        flip.addBuffer_text(row1,0,4);
    }
    else
    {
        Serial.println("Two rows");
        flip.addBuffer_text(row1,0,0);
        flip.addBuffer_text(row2,0,8);
    }

    return true;
}


bool textLargeHandler(const HomieRange& range, const String& value) 
{
    Serial.print("Text Large payload="); Serial.println(value);

    String row1=value;

    Serial.print("Row="); Serial.println(row1);
    
    flip.setBuffer_solid(0); //clear

    flip.addBuffer_text(row1,255,0,1); //large font, centered

    return true;
}

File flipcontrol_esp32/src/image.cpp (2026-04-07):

#include "image.h"

#include "fonts.h"

Image::Image()
{    
}

void Image::serialPrintInt(uint16_t source)
{
    for(uint8_t i = 0; i < 16; i++)
        Serial.print((source & (1 << i)) > 0);
}

void Image::init()
{
    flipdot.init(); //sets pin modes etc.

    flag_updating=false;
    update_counter=0;
    updateDelay=10;
    
    resetOrder(true);
}

uint8_t Image::getW() 
{
    return COLUMNS;
}

uint8_t Image::getH() 
{
    return ROWS;
}

void Image::setBuffer_solid(bool set)
{
    for (uint8_t x = 0; x < getW(); x++) 
    {
        if (set) 
            backBuffer[x]=0xffff; //all white
        else
            backBuffer[x]=0x0; //all black
    }

    flag_updating = true; //make update run
}

void Image::addBuffer_text(String text, uint8_t xoffset, uint8_t yoffset, uint8_t pfont)
{
    uint8_t font_width;
    uint8_t font_spacing;
    switch (pfont){
        case 0:
            font_width=font_normal_width;
            if (xoffset=255) { //centering?
                xoffset=(COLUMNS-text.length()*(font_normal_mean_width+font_spacing))/2;
            }
            break;
        case 1:
            font_width=font_large_width;
            if (xoffset=255) { //centering?
                xoffset=(COLUMNS-text.length()*(font_large_mean_width+font_spacing))/2;
            }
            break;
    }

    uint8_t bufferxpos=xoffset;
    for (uint8_t textpos=0;textpos<text.length();textpos++){
        
        char currentchar=text.charAt(textpos);
        Serial.print("Current Char "); Serial.print((uint8_t)currentchar); Serial.print(":"); Serial.println(currentchar);
        
        uint8_t emptycolumncounter=0; //count how many empty trailing columns for a character
        for (uint8_t x=0;x<font_width;x++) {
            uint16_t addBuffer;
            if (currentchar==' ') { //space
                addBuffer=0; //empty
            }else{
                switch (pfont) {
                    case 0:
                        addBuffer=( (uint16_t)( font_normal[(uint8_t)currentchar-font_offset][x] ) << yoffset);
                        break;
                    case 1:
                        addBuffer=( (uint16_t)( font_large[(uint8_t)currentchar-font_offset][x] ) << yoffset);
                        break;
                }

                if (addBuffer==0) {
                    emptycolumncounter++;
                }else{
                    emptycolumncounter=0; //reset
                }
            }
            backBuffer[bufferxpos]|= addBuffer;
            Serial.print("Buffer at "); Serial.print(bufferxpos); Serial.print(" add ");Serial.print(addBuffer,2); Serial.print(" result="); Serial.println(backBuffer[bufferxpos],2);

            bufferxpos++;
        }
        bufferxpos-= emptycolumncounter-font_spacing; //remove trailing empty columns except one
    }
    Serial.println("Finished Text");
}


void Image::setBuffer_Preset_Stripes()
{
    for (int i = 0; i < getW(); i++)
    {
        backBuffer[i] = (1 << (i % 16));
    }    

    flag_updating = true; //make update run
}

void Image::setBuffer_Preset_Checkers()
{
    for (int i = 0; i < getW(); i++)
    {
        if (i % 2)
            backBuffer[i] = 0xAAAA;
        else
            backBuffer[i] = 0x5555;
    }    

    flag_updating = true; //make update run
}

void Image::setBuffer_Preset_CheckersInverse()
{
    for (int i = 0; i < getW(); i++)
    {
        if (i % 2)
            backBuffer[i] = 0x5555;
        else
            backBuffer[i] = 0xAAAA;
    }    

    flag_updating = true; //make update run
}

void Image::setBufferColumn(uint8_t _colnum, uint16_t _rowdata)
{
    if (_colnum >= COLUMNS) 
    {
        Serial.println("colnum too high");
    }
    else
    {
        backBuffer[_colnum]=_rowdata; //all white

        flag_updating = true; //make update run
    }
}

void Image::setBuffer_random(uint8_t brightness)
{
    for (uint8_t x = 0; x < getW(); x++) 
    {
        uint16_t randomnumber = 0;
        
        for (uint8_t y = 0; y < getH(); y++) 
        {
            if (random(256) < brightness)  //the higher the parameter the more white
                randomnumber += pow(2, y);
        }

        backBuffer[x] = randomnumber;
    }

    flag_updating=true; //make update run
}


void Image::setBuffer_byString(String data, String& error)
{
    //first check size
    if (data.length() != getW() * getH())  //if characters matches pixels then its likely binary
        error="setBuffer_byString: size mismatch";

    for (uint8_t x = 0; x < getW(); x++) 
    {
        uint16_t columnnumber = 0;
        for (uint8_t y = 0; y < getH(); y++) 
        {
            char currentChar = data.charAt(x * getH() + y);
            if (currentChar != '0' && currentChar != ' ' && currentChar != '_') { //0, Space or "_" are black pixels.
                columnnumber += pow(2, y); //if not one of the above, then make white
            }            
        }
        backBuffer[x]=columnnumber;  
    }

    flag_updating=true; //make update run    
}

void Image::setBuffer_byInt(String data,String& error)
{
    int str_len = data.length() + 1; 
    char char_array[str_len];
    data.toCharArray(char_array, str_len);

    char *token = strtok(char_array, ",");

    uint8_t x=0;
    while (token != NULL && x<getW()) {
        String tokenString(token);
        
        uint16_t tokenInt=tokenString.toInt();
        
        backBuffer[x]=tokenInt;

        token = strtok(NULL, ","); //get next token
        x++;
    }
    if (x!=getW()) { //x reached exaclty the end
        Serial.println("Warning: Not Enough Data!");
        error="setBuffer_byInt: not enough data. x="+x;
    }
    if (token!= NULL) { //exited loop but there was another valid token
        Serial.println("Warning: too much data");
        error="setBuffer_byInt: too much data";
    }

    flag_updating=true; //make update run    
}


void Image::resetOrder(bool ascending) {
    for (uint8_t i=0;i<getW();i++) { //fill with ascending numbers
        if (ascending) {
            orderArray[i]=i;
        }else{
            orderArray[i]=(getW()-1) - i;
        }
    }
}

void Image::shuffleOrder(uint8_t iterations) 
{
    for (uint8_t s=0;s<iterations;s++) { //shuffle iterations
        uint8_t _r1=random(getW());
        uint8_t _r2=random(getW());
        uint8_t _backup=orderArray[_r1];
        //swap numbers
        orderArray[_r1]=orderArray[_r2];
        orderArray[_r2]=_backup; 
    }

    for (uint8_t i=0;i<getW();i++) { //fill with ascending numbers
        Serial.print(orderArray[i]); Serial.print(" ");
    }
    Serial.println();
}
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
